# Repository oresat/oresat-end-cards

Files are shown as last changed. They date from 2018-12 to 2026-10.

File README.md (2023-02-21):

# "End Card" PCBs for OreSat

OreSat cards in the top position (#1) and bottom position (#20) are special because they interface with
both the solar arrays and with the end caps. They also tend to hold deployable antennas.

## Features

- 4 solar panel connectors
- 3 available RF connectors
- Alternative backplane connectors only (since the solar panel connectors take up the main connector spot)

## Connector information

- TBD.

## LICENSE

Copyright Portland State Aerospace Society 2022.

This documentation describes Open Hardware and is licensed under the CERN OHL v2

You may redistribute and modify this documentation under the terms of the CERN OHL v.1.2. [https://ohwr.org/cernohl](https://ohwr.org/cernohl). This documentation is distributed WITHOUT ANY EXPRESS OR IMPLIED WARRANTY, INCLUDING OF MERCHANTABILITY, SATISFACTORY QUALITY AND FITNESS FOR A PARTICULAR PURPOSE. Please see the CERN OHL v2 for applicable conditions.

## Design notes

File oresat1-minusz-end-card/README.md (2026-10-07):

---
title: "**OreSat1 -Z End Card**"
subtitle: |
  **Fabrication and Assembly Information**\
  For build TIME-STAMP
fontsize: 10pt
geometry:
  - margin=0.5in
toc: true
toc-depth: 2
colorlinks: true
urlcolor: blue
---

\newpage

# About this Board

## Board Description

The OreSat1 -Z End Card fits in the very "bottom" slot (Slot #20?) in the OreSat1 2U backplane. It's special because it hosts whatever antenna is on the -Z face of the satellite, which in this case is an L band monopole, a UHF band monopole, and an L1 band GPS patch antenna. The -Z End Card:

- Connects to the backplane with a main connector and three RF SMPM connectors
- Connects two -Z solar modules to the backplane (two of the solar module spots are taken up by the copper radiator panels for the CFC assembly)
- Routes an SMPM connector to a U.FL connector to jump up to the -Z End Cap's L1 band GPS patch antenna
- Has an OPD circuit to control:
   - Deploying the monopole antennas
   - Switching C3-UART to any of the -Z solar modules

## Documentation Links

- -Z End Card Git repository: <https://github.com/oresat/oresat-end-cards>
- **TODO:** -Z End Card Design Notes + Design Review Notes

## Documentation Files

| Filename | Notes |
| --- | --- |
| README.pdf | This README file |
| PROJECT-NAME-outline.dxf | Board outline (with holes) in DXF format |
| PROJECT-NAME-pcba.step | 3D model of PCBA (with components) |
| PROJECT-NAME-render-bot.jpg | Render of the top of the 3D model |
| PROJECT-NAME-render-bot.jpg | Render of the bottom of the 3D model |
| PROJECT-NAME-schematic.pdf | PDF of board schematics |

## Contact Information

- Website: <https://www.oresat.org/>
- Email: <oresat@pdx.edu>
- Instagram: @pdxaerospace

## Board Renders

Render of the top of the 3D model
Render of the bottom of the 3D model

\newpage

# Printed Circuit Board (PCB) Fabrication Information

## Board Info

- 4 layer board
- Bounding box is 99.8 x 94.6 mm (3.93 x 3.72 in)
- Board thickness is 1.59 mm (0.063 inch)
- **Important:** See Materials and Stack Up sections below

## Board Requirements

- Design Rules
    - Minimum Trace / Space design rules
       - Outer layers: 0.127 mm (5.0 mil) / 0.127 mm (5.0 mil)
       - Inner layers: 0.127 mm (5.0 mil) / 0.127 mm (5.0 mil)
    - Outer dimension router tolerance: +/- 0.254 mm (10.0 mil)
    - Hole placement tolerance: +/- 0.075 mm (3.0 mil)
    - Inner tab routed slot tolerance: +/- 0.254 mm (10.0 mil)
- Drills
   - Drill Positional Tolerance: 0.051 mm (2.0 mil)
   - Drill Size tolerance: +/- 0.064 mm (2.5 mil)
- Plated/Un-plated holes
  - There are 16 un-plated (NPT) holes
  - There are 434 plated through (PTH) holes
  - PTH minimum diameter: 0.254 mm (10 mil)
  - PTH minimum annulus: 0.102 mm (4 mil) radius
- Outline/Routing
  - Requires a 1.0 mm or smaller diameter routing bit
- Slots
  - There are two 1.0 mm plated slots.
- Cutouts
  - There is are two cutouts.
- There are 3 fiducials on the top layer and 3 fiducials on the bottom layer.
- Panel tabs ("mouse bites")
   - Card edges must be smooth; no mouse bites or other intrusions into the card outline.
   - If external mouse bites are required, minimize and customer will remove by hand before assembly.
- If not otherwise specified, build to IPC 6012 Class 2 or better.

## Materials

- Controlled impedance
   - The stackup is critical for the performance of high speed signals on this board.
   - As long as the stackup is controlled, the board is not considered controlled impedance.
- Isola FR408HR or material with equivalent Dk.
- Board Surface treatment should be ENIG, althogh immersion Silver is acceptable.
- White silkscreen on top and bottom surface
- Taiyo PSR-4000 or equivalent soldermask on top and bottom, no requirements for color.

## Stack Up

| Layer | Thickness | Notes |
|---|---|---|
| Top Copper | 0.043 mm /  1.7 mil |  Layer 1 foil, 1 oz Cu after plating |
| prepreg | 0.200 mm /  7.9 mil |  Prepreg - Isola FR408HR 2113 |
| Layer 2 | 0.018 mm /  0.7 mil |  Layer 2 foil, 0.5 oz Cu |
| Core | 0.991 mm / 39 mil |  Core Isola FR408HR |
| Layer 3 | 0.018 mm /  0.7 mil |  Layer 3 foil, 0.5 oz Cu |
| prepreg | 0.200 mm /  7.9 mil |  Prepreg - Isola FR408HR 2113 |
| Bottom Copper | 0.043 mm /  1.7 mil |  Layer 4 foil, 1 oz copper after plating |
| **Total Stackup** | **1.588 mm / 62.5 mil** | |

## Array / Panel Information

- Coordinate with Contract Manufacturer (CM) for optimal size of this panel.
- If no feedback from CM, then produce single boards (no panel).

## Fabrication Files

### IPC-2581 File

| Filename | Notes |
| --- | --- |
| PROJECT-NAME-ipc2581.xml | IPC-2581 board information file |

### Legacy PCB Files

| Filename | Notes |
| ---| --- |
| PROJECT-NAME-Edge_Cuts.gbr | RS274X file for the dimension (outline) layer |
| PROJECT-NAME-F_Silkscreen.gbr | RS274X file for the top silkscreen |
| PROJECT-NAME-F_Mask.gbr | RS274X file for the top soldermask |
| PROJECT-NAME-F_Cu.gbr | RS274X file for the top copper layer |
| PROJECT-NAME-In1_Cu.gbr | RS274X file for the layer 2 copper |
| PROJECT-NAME-In2_Cu.gbr | RS274X file for the layer 3 copper |
| PROJECT-NAME-B_Cu.gbr | RS274X file for the bottom copper layer |
| PROJECT-NAME-B_Mask.gbr | RS274X file for the bottom soldermask |
| PROJECT-NAME-B_Silkscreen.gbr | RS274X file for the bottom silkscreen |
| PROJECT-NAME-NPTH.drl | Excellon file for non-plated through holes |
| PROJECT-NAME-PTH.drl | Excellon file for plated through holes | 

\newpage

# Printed Circuit Board Assembly (PCBA) Information

## Assembly Info

- Components are on the top and bottom side of the board.
- This PCBA is mostly surface mount (SMT) with a few (THT) components.

## Assembly Requirements

- Assemble to IPC Class 2 or better
- Bake components that are not moisture sealed to appropriate levels as required.
- Solder paste MUST be leaded.
- Aqueous flux and wash strongly preferred.
   - Clean to NASA Standard "Visibly Clean (VC)": No particles or residues are visible to the naked eye.
- No conformal coating.
- Ship in antistatic protective bag

## Component Specific Assembly Information

- SMPM connectors (CM1 - CM3) should be hand-addedaccording to SOP (there is no solder paste for their footprints).
- Monopole antennas must be hand added according to the Antenna SOP.
- Resistor R1 must be hand added according to the OreSat End Card Deployment Resistor Mounting SOP.
- Press fit nuts HW1 - HW6 may be *carefully* added after SMT assembly is completed.

## Assembly Files

### IPC-2581 File

| Filename | Notes |
| --- | --- |
| PROJECT-NAME-ipc2581.xml | IPC-2581 board information file |

### Bill of Materials (BOM)

| Filename | Description |
| --- | --- |
| PROJECT-NAME-bom.csv | BOM in Comma Separated Variable format |

### Solder Paste Stencils

| Filename | Notes |
| --- | --- |
| PROJECT-NAME-B_Paste.gbr | RS274X file for top/front solder paste stencil |
| PROJECT-NAME-F_Paste.gbr | RS274X file for bottom/back solder paste stencil |

### Mounting/Placement Location

| Filename | Description |
| --- | --- |
| PROJECT-NAME-3u.pos | Pick and place locations for components |

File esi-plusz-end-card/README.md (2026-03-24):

---
title: "**OreSat1 +Z End Card**"
subtitle: |
  **Fabrication and Assembly Information**\
  For build TIME-STAMP
fontsize: 10pt
geometry:
  - margin=0.5in
toc: true
toc-depth: 2
colorlinks: true
urlcolor: blue
---

\newpage

# About this Board

## Board Description

The +Z End Card fits in the very "top" slot (Slot #1) in the OreSat backaplane. It's special because it hosts whatever antenna is on the +Z face, and also interfaces with the solar modules on the +Z "U" of the CubeSat. The +Z End Card:

- Connects to the backplane with a main connector and two RF SMPM connectors
- Connects four +Z solar modules to the backplane
- Mounts and matches to the S band helical antenna
- Routes an SMPM connector to a U.FL connector to jump up to the +Z End Cap's S band patch antenna
- Has an OPD circuit to control:
   - Deploying the helical antenna
   - Switching C3-UART to any of the +Z solar modules

## Documentation Links

- +Z End Card Git repository: <https://github.com/oresat/oresat-end-cards>
- **TODO:** +Z End Card Design Notes + Design Review Notes

## Documentation Files

| Filename | Notes |
| --- | --- |
| README.pdf | This README file |
| PROJECT-NAME-outline.dxf | Board outline (with holes) in DXF format |
| PROJECT-NAME-pcba.step | 3D model of PCBA (with components) |
| PROJECT-NAME-render-bot.jpg | Render of the top of the 3D model |
| PROJECT-NAME-render-bot.jpg | Render of the bottom of the 3D model |
| PROJECT-NAME-schematic.pdf | PDF of board schematics |

## Contact Information

- Website: <https://www.oresat.org/>
- Email: <oresat@pdx.edu>
- Instagram: @pdxaerospace

## Board Renders

Render of the top of the 3D model
Render of the bottom of the 3D model

\newpage

# Printed Circuit Board (PCB) Fabrication Information

## Board Info

- 4 layer board
- Bounding box is 99.8 x 94.6 mm (3.93 x 3.72 in)
- Board thickness is 1.59 mm (0.063 inch)
- **Important:** See Materials and Stack Up sections below

## Board Requirements

- Design Rules
    - Minimum Trace / Space design rules
       - Outer layers: 0.127 mm (5.0 mil) / 0.127 mm (5.0 mil)
       - Inner layers: 0.127 mm (5.0 mil) / 0.127 mm (5.0 mil)
    - Outer dimension router tolerance: +/- 0.254 mm (10.0 mil)
    - Hole placement tolerance: +/- 0.075 mm (3.0 mil)
    - Inner tab routed slot tolerance: +/- 0.254 mm (10.0 mil)
- Drills
   - Drill Positional Tolerance: 0.051 mm (2.0 mil)
   - Drill Size tolerance: +/- 0.064 mm (2.5 mil)
- Plated/Un-plated holes
  - There are 35 un-plated (NPT) holes
  - There are 454 plated through (PTH) holes
  - PTH minimum diameter: 0.254 mm (10 mil)
  - PTH minimum annulus: 0.102 mm (4 mil) radius
- Outline/Routing
  - Requires a 1.0 mm or smaller diameter routing bit
- Slots
  - There are no slots.
- Cutouts
  - There is one cutout
- There are 3 fiducials on the top layer.
- Panel tabs ("mouse bites")
   - Card edges must be smooth; no mouse bites or other intrusions into the card outline.
   - If external mouse bites are required, minimize and customer will remove by hand before assembly.
- If not otherwise specified, build to IPC 6012 Class 2 or better.

## Materials

- Controlled impedance
   - The stackup is critical for the performance of high speed signals on this board.
   - As long as the stackup is controlled, the board is not considered controlled impedance.
- Isola FR408HR or material with equivalent Dk.
- Board Surface treatment should be ENIG, althogh immersion Silver is acceptable.
- White silkscreen on top and bottom surface
- Taiyo PSR-4000 or equivalent soldermask on top and bottom, no requirements for color.

## Stack Up

| Layer | Thickness | Notes |
|---|---|---|
| Top Copper | 0.043 mm /  1.7 mil |  Layer 1 foil, 1 oz Cu after plating |
| prepreg | 0.200 mm /  7.9 mil |  Prepreg - Isola FR408HR 2113 |
| Layer 2 | 0.018 mm /  0.7 mil |  Layer 2 foil, 0.5 oz Cu |
| Core | 0.991 mm / 39 mil |  Core Isola FR408HR |
| Layer 3 | 0.018 mm /  0.7 mil |  Layer 3 foil, 0.5 oz Cu |
| prepreg | 0.200 mm /  7.9 mil |  Prepreg - Isola FR408HR 2113 |
| Bottom Copper | 0.043 mm /  1.7 mil |  Layer 4 foil, 1 oz copper after plating |
| **Total Stackup** | **1.588 mm / 62.5 mil** | |

## Array / Panel Information

- Coordinate with Contract Manufacturer (CM) for optimal size of this panel.
- If no feedback from CM, then produce single boards (no panel).

## Fabrication Files

### IPC-2581 File

| Filename | Notes |
| --- | --- |
| PROJECT-NAME-ipc2581.xml | IPC-2581 board information file |

### Legacy PCB Files

| Filename | Notes |
| ---| --- |
| PROJECT-NAME-Edge_Cuts.gbr | RS274X file for the dimension (outline) layer |
| PROJECT-NAME-F_Silkscreen.gbr | RS274X file for the top silkscreen |
| PROJECT-NAME-F_Mask.gbr | RS274X file for the top soldermask |
| PROJECT-NAME-F_Cu.gbr | RS274X file for the top copper layer |
| PROJECT-NAME-In1_Cu.gbr | RS274X file for the layer 2 copper |
| PROJECT-NAME-In2_Cu.gbr | RS274X file for the layer 3 copper |
| PROJECT-NAME-B_Cu.gbr | RS274X file for the bottom copper layer |
| PROJECT-NAME-B_Mask.gbr | RS274X file for the bottom soldermask |
| PROJECT-NAME-B_Silkscreen.gbr | RS274X file for the bottom silkscreen |
| PROJECT-NAME-NPTH.drl | Excellon file for non-plated through holes |
| PROJECT-NAME-PTH.drl | Excellon file for plated through holes | 

\newpage

# Printed Circuit Board Assembly (PCBA) Information

## Assembly Info

- All components are on the top side of the board.
- This PCBA is mostly surface mount (SMT) with a few (THT) components.

## Assembly Requirements

- Assemble to IPC Class 2 or better
- Bake components that are not moisture sealed to appropriate levels as required.
- Solder paste MUST be leaded.
- Aqueous flux and wash strongly preferred.
   - Clean to NASA Standard "Visibly Clean (VC)": No particles or residues are visible to the naked eye.
- No conformal coating.
- Ship in antistatic protective bag

## Component Specific Assembly Information

- SMPM connectors (CM1, CM2) should be hand-added (there is no solder paste for their footprints).
- HELICAL_ANT must be hand added according to the Helical Antenna SOP.
- Resistor R1 must be hand added according to the OreSat End Card Deployment Resistor Mounting SOP.
- Press fit nuts may be *carefully* added after SMT assembly is completed, although it's better if they're added before assembly.

## Assembly Files

### IPC-2581 File

| Filename | Notes |
| --- | --- |
| PROJECT-NAME-ipc2581.xml | IPC-2581 board information file |

### Bill of Materials (BOM)

| Filename | Description |
| --- | --- |
| PROJECT-NAME-bom.csv | BOM in Comma Separated Variable format |

### Solder Paste Stencils

| Filename | Notes |
| --- | --- |
| PROJECT-NAME-B_Paste.gbr | RS274X file for top/front solder paste stencil |
| PROJECT-NAME-F_Paste.gbr | RS274X file for bottom/back solder paste stencil |

### Mounting/Placement Location

| Filename | Description |
| --- | --- |
| PROJECT-NAME-3u.pos | Pick and place locations for components |

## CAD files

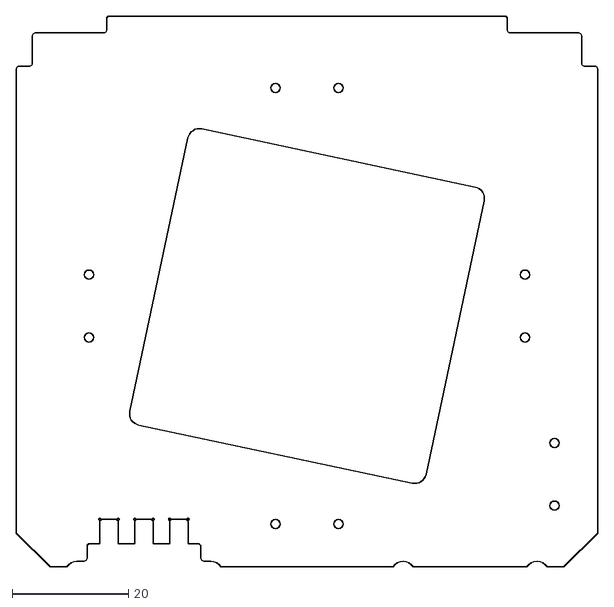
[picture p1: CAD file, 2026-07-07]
esi-plusz-end-card/Endcard PCB for beecon.dxf
99.8 x 94.6

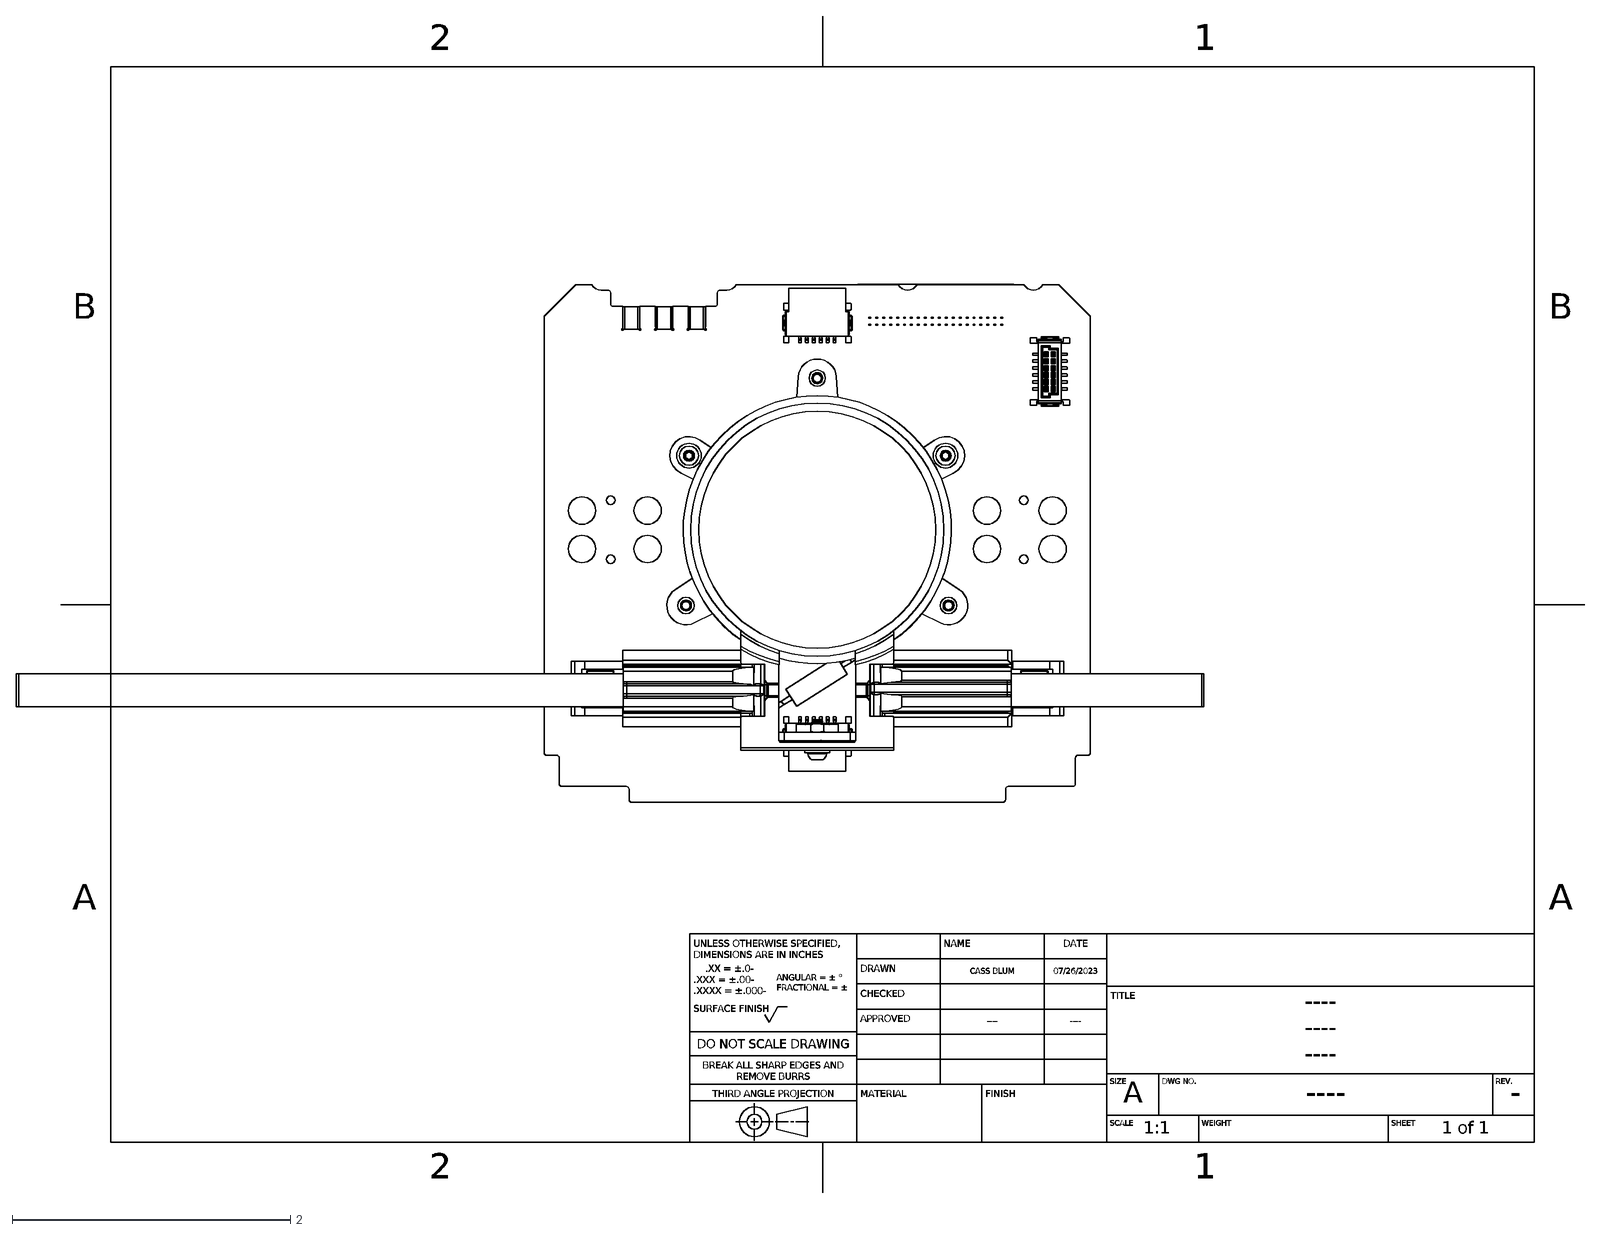
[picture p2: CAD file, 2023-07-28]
oresat0.5-minusz-end-card/oresat0.5-minusz-end-card.dxf
2
1
A
B
UNLESS OTHERWISE SPECIFIED, DIMENSIONS ARE IN INCHES
.XX = ±.0- .XXX = ±.00- .XXXX = ±.000-
ANGULAR = ± ° FRACTIONAL = ±
SURFACE FINISH
DO NOT SCALE DRAWING
BREAK ALL SHARP EDGES AND REMOVE BURRS
THIRD ANGLE PROJECTION
NAME
DATE
DRAWN
CASS BLUM
07/26/2023
CHECKED
APPROVED
----
MATERIAL
FINISH
TITLE
SIZE
DWG NO.
REV.
-
SCALE
1:1
WEIGHT
SHEET
1 of 1

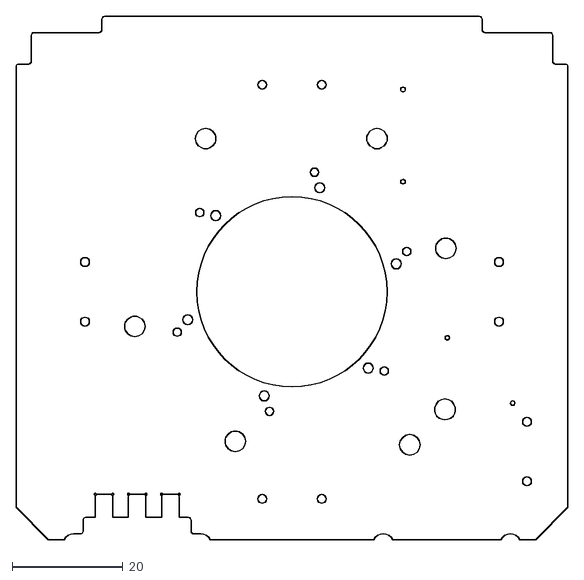
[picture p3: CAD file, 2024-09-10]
oresat0.5-plusz-end-card/Endcard PCBs - Endcard PCB (1).dxf
99.8 x 94.6

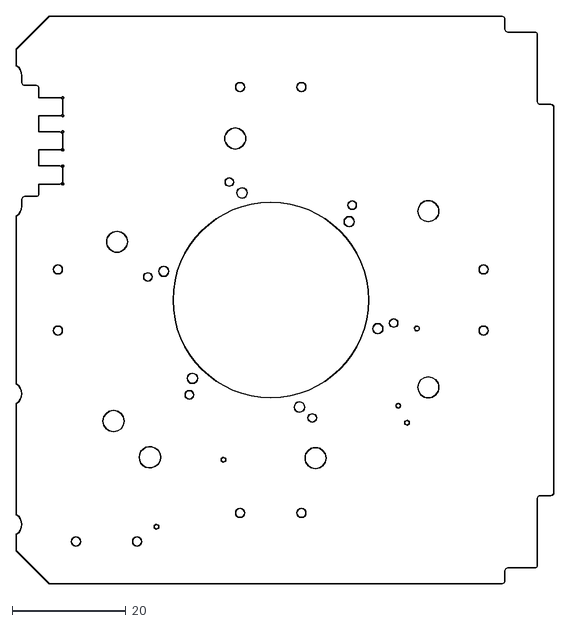
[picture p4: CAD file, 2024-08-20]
oresat0.5-plusz-end-card/oresat0.5-pluz-end-card.dxf
94.6 x 99.8

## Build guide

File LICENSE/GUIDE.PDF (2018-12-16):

# Guide to the CERN OHL v.1.2

This document contains guidelines on how to apply the CERN OHL v.1.2 to a given hardware design, and on the use of hardware designs licensed under the CERN OHL v.1.2.

How to apply the CERN OHL v.1.2 to a hardware design Pre-requisite:

Authorship/ownership of the design must be clear and undisputed. Only the legal owner of the rights in the hardware design may decide under what conditions to make it available. If ownership is vested in more than one person/entity, there must be an agreement among the owners to release the hardware design as open hardware, and under the CERN OHL in particular.

The hardware design documentation and files package

Pack all your hardware design documentation files (schematics, layout...) as well as the documents listed below in an archive file. This will ensure the licensee downloads everything in one go. It is best to archive the files using a format everybody can open. Schematics and layouts should be included in both source form and a format readable by everybody, such as pdf.

The following documents must be distributed together with the hardware design documentation:

- Document containing the CERN OHL v.1.2 (e.g. LICENSE.PDF)
- This Guide
- Text files (plain ASCII file), where information can be added to but not removed from, listing:
- Contact point wishing to receive information about manufactured Products (see section 4.2) (e.g. PRODUCT.TXT);
- Modifications made by Licensee (see section 3.4.b) (e.g. CHANGES.TXT)

What to do with the hardware design documentation

Include in the hardware design documentation, for instance as a header, the following elements (see section 3.1 CERN OHL v.1.2):
- a copyright notice reflecting actual ownership;
- a notice that the hardware design documentation is licensed under the CERN OHL v.1.2, possibly with a link to http://ohwr.org/cernohl where the licence texts are hosted:
- “Licensed under CERN OHL v.1.2 or later”
- “Licensed under CERN OHL v.1.2”;
- a disclaimer of warranties;
- a Documentation Location if you wish to specify one;

The following is an example of header if CERN is the Licensor:

Copyright CERN 2013.

This documentation describes Open Hardware and is licensed under the CERN OHL v. 1.2.

You may redistribute and modify this documentation under the terms of the CERN OHL v.1.2. (http://ohwr.org/cernohl). This documentation is distributed WITHOUT ANY EXPRESS OR IMPLIED WARRANTY, INCLUDING OF MERCHANTABILITY, SATISFACTORY QUALITY AND FITNESS FOR A PARTICULAR PURPOSE. Please see the CERN OHL v.1.2 for applicable conditions

Include in a part of the Documentation corresponding to a visible part of the Product (e.g. silkscreen or top copper for a Printed Circuit Board):

- the licence notice: “Licensed under CERN OHL v.1.2”
- Do not include the CERN logo or the copyright notice
- the Documentation Location if you wish it to appear on the Product, thus enabling all subsequent recipients of the Products to find the Documentation.

How to deal with hardware designs licensed under the CERN OHL v.1.2
Generally speaking, you must always comply with any obligations applying to a particular design (detailed in a contract or accompanying licence). If you receive hardware designs licensed under the CERN OHL v.1.2, the obligations are to:
- Keep intact all the copyright and trademark notices and Documentation Location notices that are on the hardware design documentation;
- Keep intact the references to the CERN OHL v.1.2;
- Keep intact the disclaimer of warranties.

If you modify hardware design that you received from someone else that is licensed under the CERN OHL v.1.2, you must

- Keep intact all the notices referred to above;
- Include notices that you have modified the hardware designs, detailing what modifications where made (e.g. in a CHANGES.TXT file);
- Add the appropriate copyright notice and Documentation Location to the modifications that were made;
- license the modifications under the CERN OHL v.1.2 if you distribute them.

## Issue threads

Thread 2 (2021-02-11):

50 ohm resistors are too big

davidalay, 2021-02-11:
footprint is 0805, should be 0603

Closed 2021-04-08.

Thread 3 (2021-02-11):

Bigger burn resistor package

davidalay, 2021-02-11:
Footprint for the burnwire resistor should be bigger, have larger drill holes, and oblong pads.  Also add second set of vias so we can J-bend the leads

Closed 2021-04-08.

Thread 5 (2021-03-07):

Move the antenna holes to center the holes on the tape spring antennas.

andrewgreenberg, 2021-03-07:
Bonus points if the mezzanine board doesn't have to be modified.

Closed 2021-04-08.

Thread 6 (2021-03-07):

Change melt wire resistor to 7.2 ohms

andrewgreenberg, 2021-03-07:
A 7.2 ohm melt wire resistor is 5 W at 6V and 10W at 8.4V.

Closed 2021-04-08.

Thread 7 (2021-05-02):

Fix the melt wire resistor and mezzanine board hybrids interference -- probably rev the placement of the hybrids on the mezzanine, not the footprint of the melt wire resistor.

davidalay, 2021-05-02:

Closed 2021-11-04.

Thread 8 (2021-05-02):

Larger annular ring around the wires (if it doesn't screw with RF stuff)

davidalay, 2021-05-02:

Closed 2021-11-04.

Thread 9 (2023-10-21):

Update all M2 press-fit nuts from a 3.7 mm to 4.0 mm hole

andrewgreenberg, 2023-10-21:
... which still is press fit, but doesn't pook out the board.

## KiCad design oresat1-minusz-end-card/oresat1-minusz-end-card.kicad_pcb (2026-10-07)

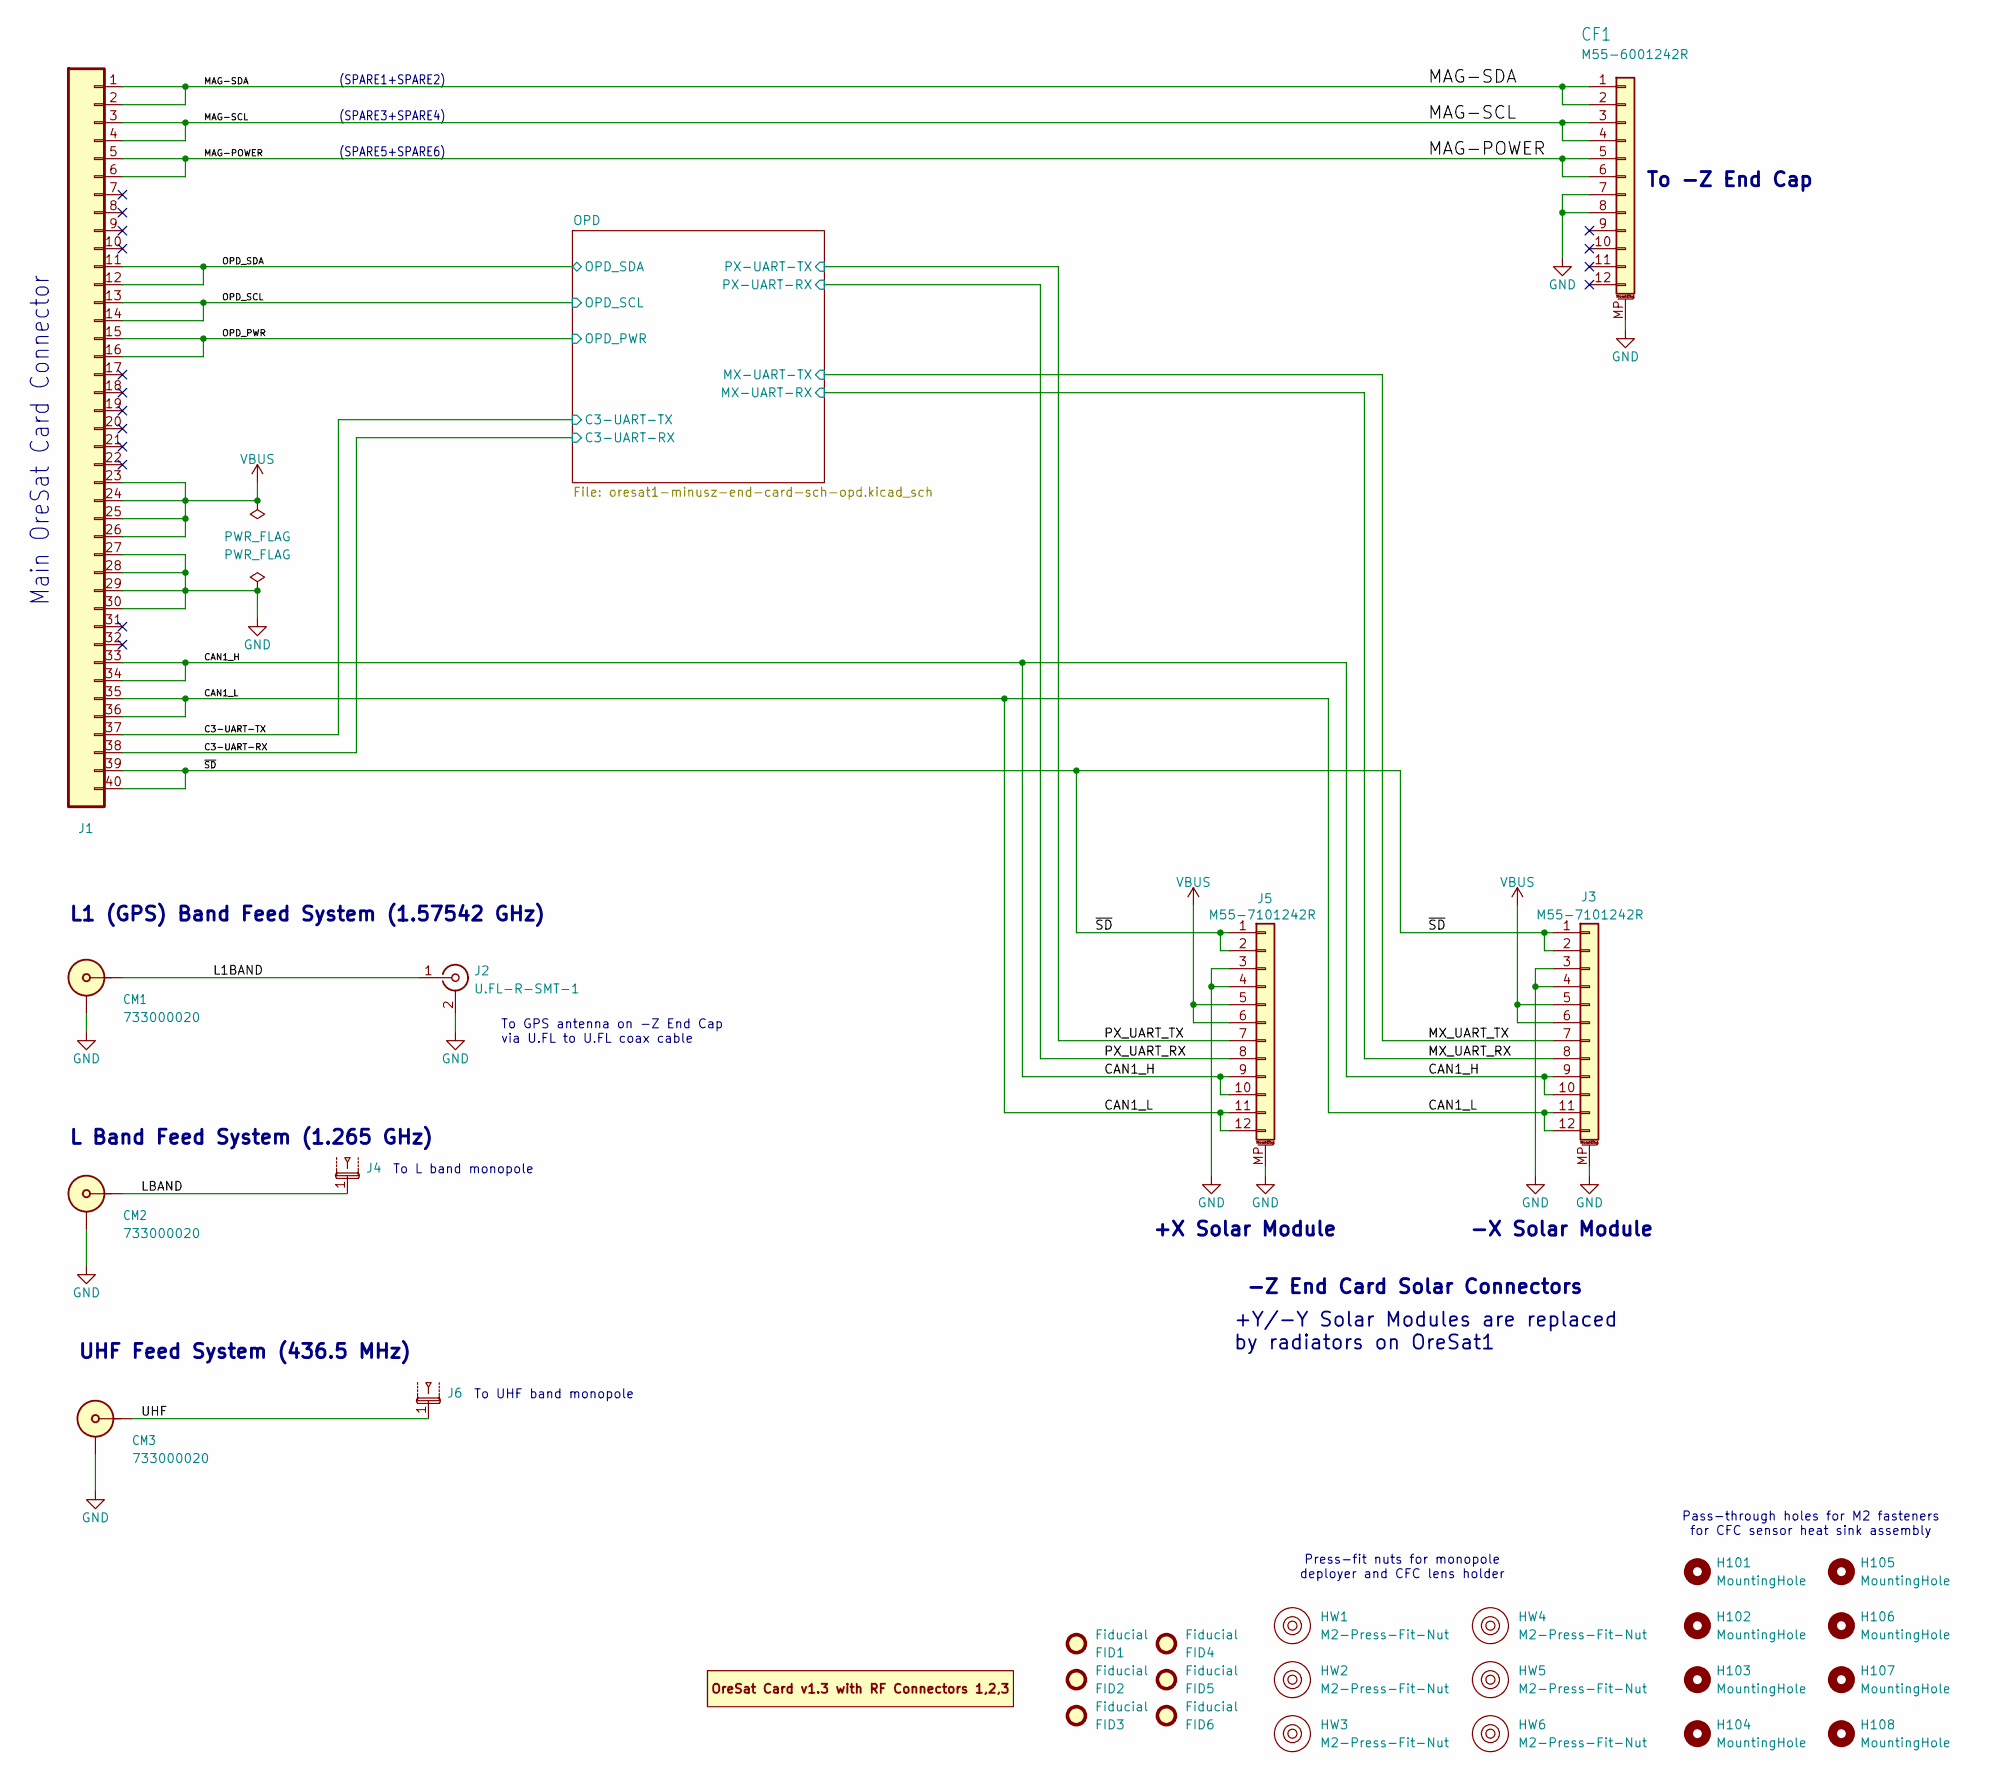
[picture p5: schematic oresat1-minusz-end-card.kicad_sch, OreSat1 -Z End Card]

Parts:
CF1: M55-6001242R; J-Harwin-M55-60X1242R; MPN M55-6001242R
CM1, CM2, CM3: 733000020; J-MOLEX-SMPM-073300-002X; MPN 2477330-1
FID1, FID2, FID3, FID4, FID5, FID6: Fiducial; Fiducial_1mm_Mask2mm
H101, H102, H103, H104, H105, H106, H107, H108: MountingHole; MountingHole_5mm
HW1, HW2, HW3, HW4, HW5, HW6: M2-Press-Fit-Nut; MPN N/A
J1: J-SAMTEC-TFM-120-01-L-D-RA; J-SAMTEC-TFM-120-X1-XXX-D-RA; MPN TFM-120-01-L-D-RA
J2: U.FL-R-SMT-1; U.FL_Hirose_U.FL-R-SMT-1_Vertical; MPN U.FL-R-SMT-1(10)
J3, J5: M55-7101242R; J-Harwin-M55-7101242R; MPN M55-7101242R
J4, J6: tape-measure-slot-antenna
PCB1: ORESAT-CARD-V1.3-GENERIC-3RF; ORESAT-CARD-V1.3-3RF

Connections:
/C3-UART-RX: J1.38; also elsewhere on the board
/C3-UART-TX: J1.37; also elsewhere on the board
/CAN1_H: J1.33, J1.34, J3.9, J3.10, J5.9, J5.10
/CAN1_L: J1.35, J1.36, J3.11, J3.12, J5.11, J5.12
/L1BAND: CM1.1 (SIG), J2.1 (In)
/LBAND: CM2.1 (SIG), J4.1
/MAG-POWER: CF1.5, CF1.6, J1.5, J1.6
/MAG-SCL: CF1.3, CF1.4, J1.3, J1.4
/MAG-SDA: CF1.1, CF1.2, J1.1, J1.2
/MX_UART_RX: J3.8; also elsewhere on the board
/MX_UART_TX: J3.7; also elsewhere on the board
/OPD_PWR: J1.15, J1.16; also elsewhere on the board
/OPD_SCL: J1.13, J1.14; also elsewhere on the board
/OPD_SDA: J1.11, J1.12; also elsewhere on the board
/PX_UART_RX: J5.8; also elsewhere on the board
/PX_UART_TX: J5.7; also elsewhere on the board
/UHF: CM3.1 (SIG), J6.1
/~SD: J1.39, J1.40, J3.1, J3.2, J5.1, J5.2
GND: CF1.7, CF1.8, CF1.MP (MountPin), CM1.2 (SHLD), CM2.2 (SHLD), CM3.2 (SHLD), J1.27, J1.28, J1.29, J1.30, J2.2 (Ext), J3.3, J3.4, J3.MP (MountPin), J5.3, J5.4, J5.MP (MountPin); also elsewhere on the board
VBUS: J1.23, J1.24, J1.25, J1.26, J3.5, J3.6, J5.5, J5.6; also elsewhere on the board

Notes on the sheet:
(SPARE5+SPARE6)
(SPARE3+SPARE4)
-Z End Card Solar Connectors
Pass-through holes for M2 fasteners for CFC sensor heat sink assembly
To L band monopole
+Y/-Y Solar Modules are replaced by radiators on OreSat1
+X Solar Module
Main OreSat Card Connector
Press-fit nuts for monopole deployer and CFC lens holder
To UHF band monopole
(SPARE1+SPARE2)
UHF Feed System (436.5 MHz)
L1 (GPS) Band Feed System (1.57542 GHz)
To -Z End Cap
To GPS antenna on -Z End Cap via U.FL to U.FL coax cable
L Band Feed System (1.265 GHz)
-X Solar Module

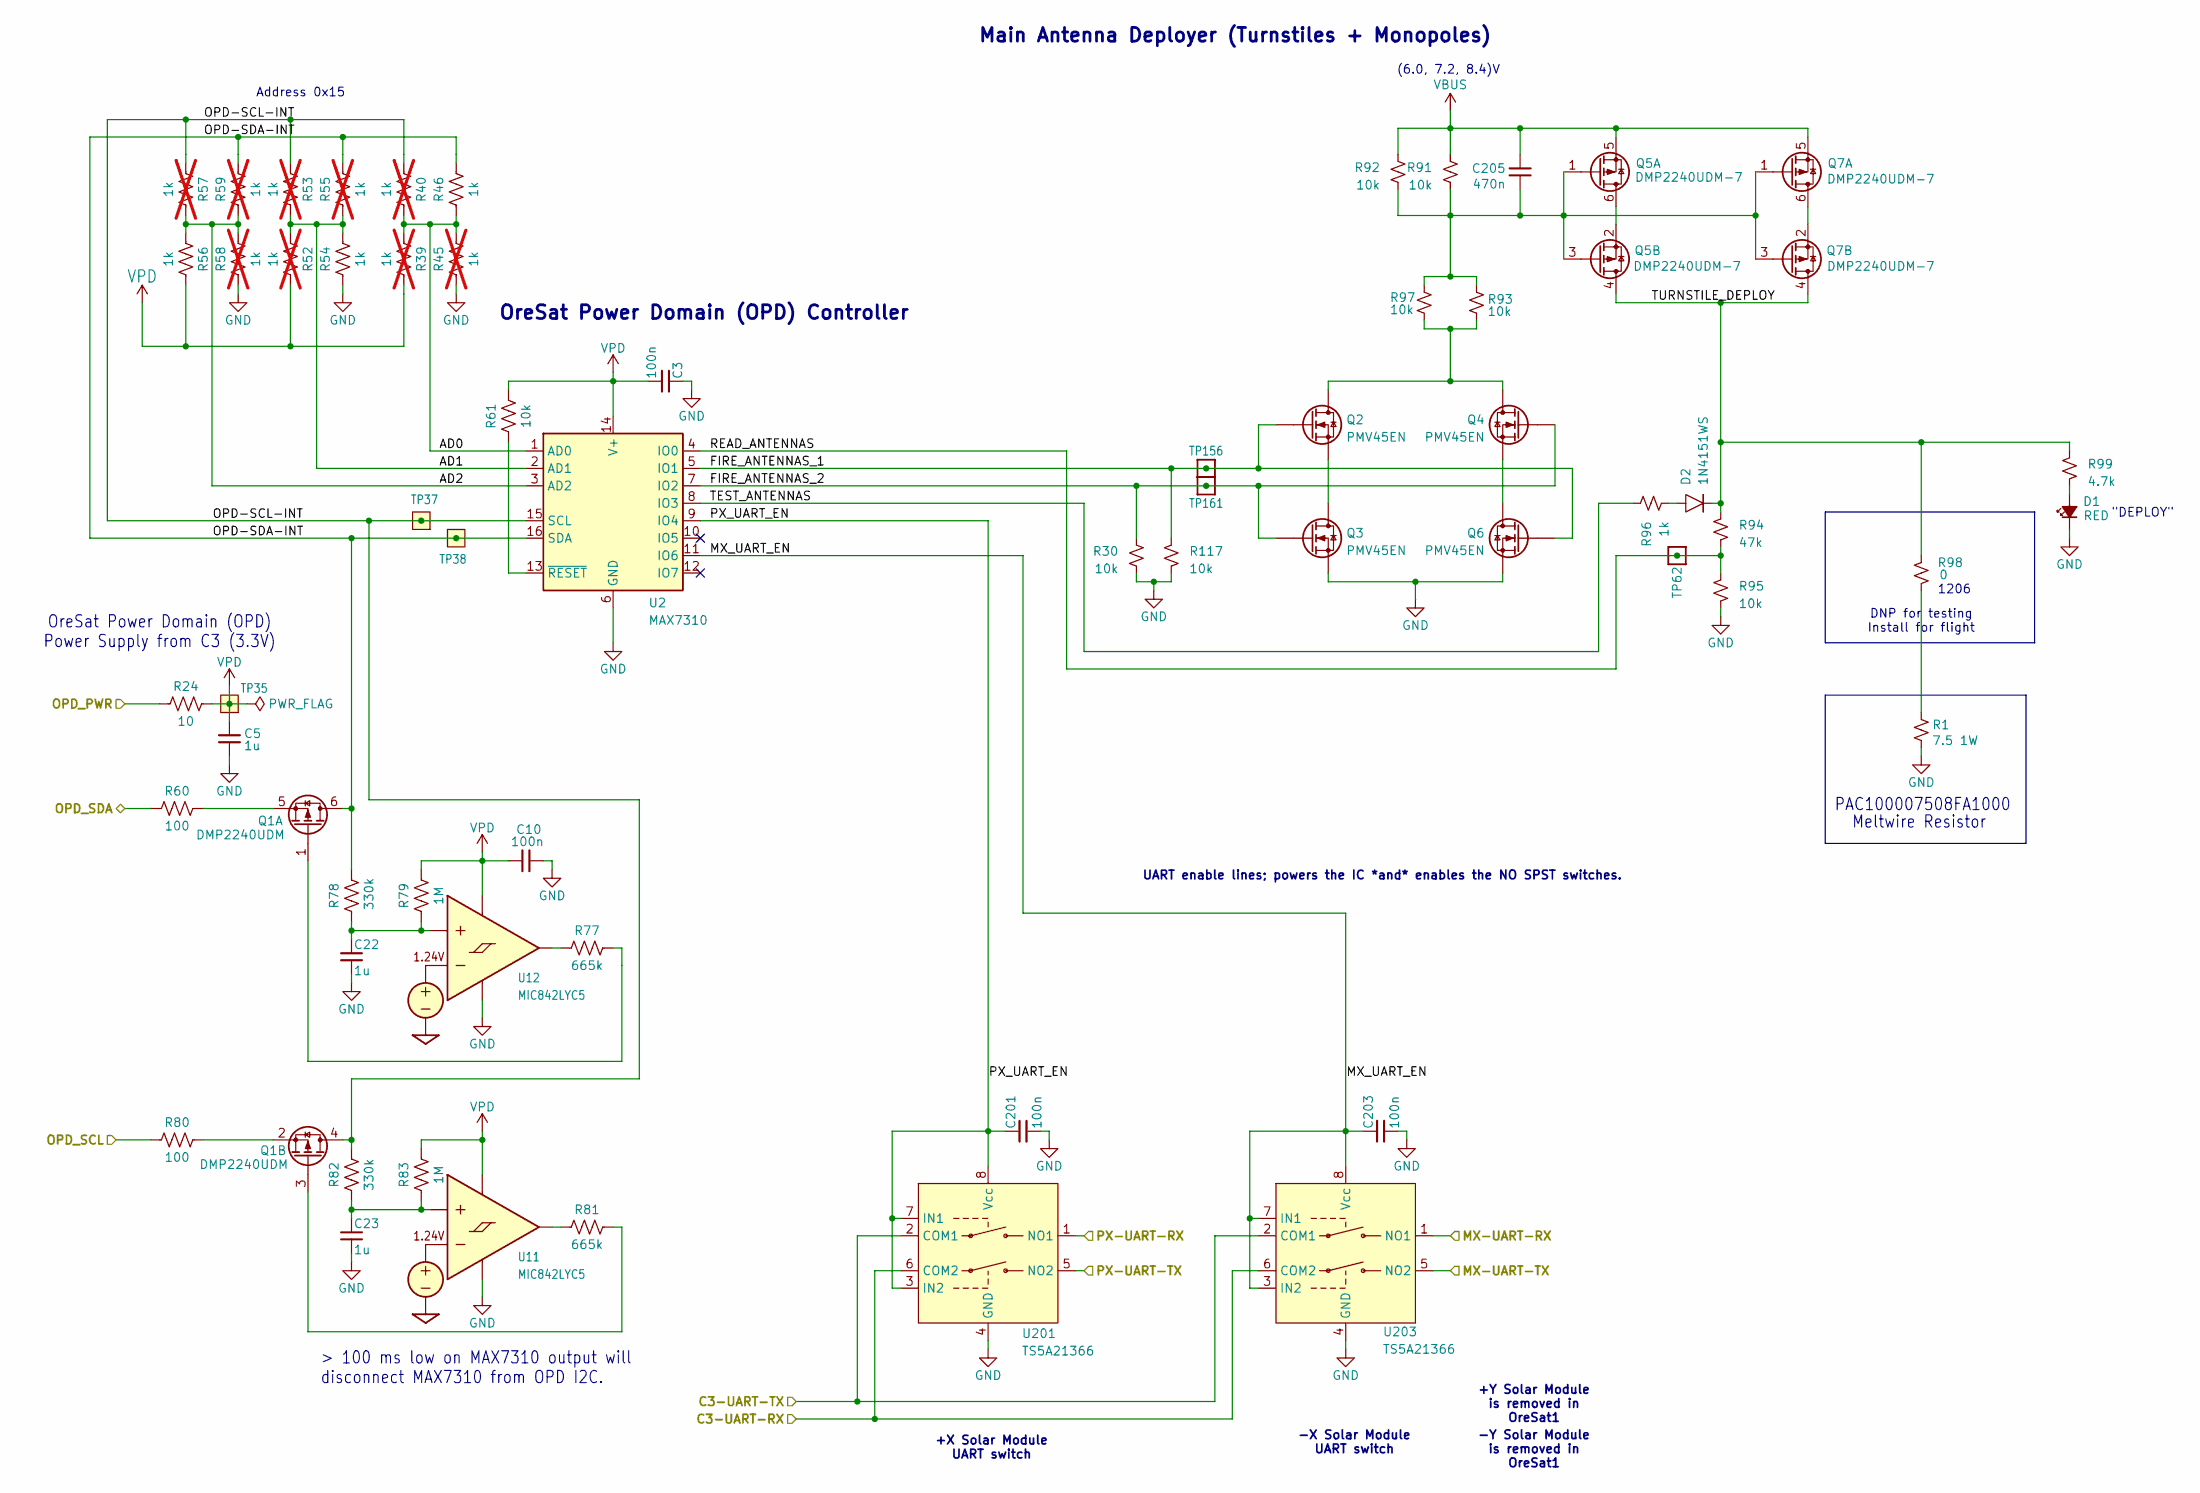
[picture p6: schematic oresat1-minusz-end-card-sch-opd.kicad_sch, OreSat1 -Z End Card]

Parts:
C3, C10, C201, C203: 100n; 0603-C-NOSILK; MPN C0603C104K5RACAUTO
C5, C22, C23: 1u; 0603-C-NOSILK; MPN GRT188R71E105KE13D
C205: 470n; 0603-C-NOSILK; MPN C0603C474K3RACAUTO
D1: RED; LED_0603_1608Metric; MPN 150060RS75000
D2: 1N4151WS; D_SOD-323; MPN 1N4151WS-E3-08
Q1: DMP2240UDM; SOT-23-6; MPN DMP2240UDM
Q2, Q3, Q4, Q6: PMV45EN; SOT-23-3; MPN PMV45EN2R
Q5, Q7: DMP2240UDM-7; SOT-23-6; MPN DMP2240UDM
R1: 7.5 1W; R-PAC100-FOR-MELTWIRE; MPN PAC100007508FA1000
R24: 10; 0603-C-NOSILK; MPN RMCF0603FT10R0
R30, R61, R91, R92, R93, R95, R97, R117: 10k; 0603-C-NOSILK; MPN RMCF0603FT10K0
R39, R40, R45, R52, R53, R55, R57, R58, R59: 1k; 0603-C-NOSILK; MPN RMCF0603FT1K00; not fitted
R46, R54, R56, R96: 1k; 0603-C-NOSILK; MPN RMCF0603FT1K00
R60, R80: 100; 0603-C-NOSILK; MPN RMCF0603FT100R
R77, R81: 665k; 0603-C-NOSILK; MPN RMCF0603FT665K
R78, R82: 330k; 0603-C-NOSILK; MPN RMCF0603FT330K
R79, R83: 1M; 0603-C-NOSILK; MPN RMCF0603FT1M00
R94: 47k; 0603-C-NOSILK; MPN RMCF0603FT47K0
R98: 0; 1206-C; MPN RMCF1206ZG0R00
R99: 4.7k; 0603-C-NOSILK; MPN RMCF0603FT4K70
TP35, TP37, TP38: Test-Point; TestPoint-0.75mm-th
TP62, TP156, TP161: Test-Point; TestPoint_Pad_D1.0mm
U2: MAX7310; QFN-16-1EP_4x4mm_P0.65mm_EP2.1x2.1mm; MPN MAX7310ATE+
U11, U12: MIC842LYC5; SOT-353_SC-70-5; MPN MIC842LYC5-TR
U201, U203: TS5A21366; VSSOP-8_2.3x2mm_P0.5mm; MPN TS5A21366DCUR

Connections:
/C3-UART-RX: U201.6 (COM2), U203.6 (COM2); also elsewhere on the board
/C3-UART-TX: U201.2 (COM1), U203.2 (COM1); also elsewhere on the board
/MX_UART_RX: U203.1 (NO1); also elsewhere on the board
/MX_UART_TX: U203.5 (NO2); also elsewhere on the board
/OPD/AD0: R39.1, R40.2, R45.2, R46.1, U2.1 (AD0)
/OPD/AD1: R52.1, R53.2, R54.2, R55.1, U2.2 (AD1)
/OPD/AD2: R56.1, R57.2, R58.2, R59.1, U2.3 (AD2)
/OPD/FIRE_ANTENNAS_1: Q2.1 (G), Q6.1 (G), R117.1, TP156.1 (1_1), U2.5 (IO1)
/OPD/FIRE_ANTENNAS_2: Q3.1 (G), Q4.1 (G), R30.1, TP161.1 (1_1), U2.7 (IO2)
/OPD/MX_UART_EN: C203.1, U2.11 (IO6), U203.3 (IN2), U203.7 (IN1), U203.8 (Vcc)
/OPD/OPD-SCL-INT: Q1.4 (D), R40.1, R53.1, R57.1, R82.2, TP37.1 (1_1), U2.15 (SCL)
/OPD/OPD-SDA-INT: Q1.6 (D), R46.2, R55.2, R59.2, R78.2, TP38.1 (1_1), U2.16 (SDA)
/OPD/PX_UART_EN: C201.1, U2.9 (IO4), U201.3 (IN2), U201.7 (IN1), U201.8 (Vcc)
/OPD/READ_ANTENNAS: R94.2, R95.1, TP62.1 (1_1), U2.4 (IO0)
/OPD/TEST_ANTENNAS: R96.1, U2.8 (IO3)
/OPD/TURNSTILE_DEPLOY: D2.1, Q5.4 (D), Q7.4 (D), R94.1, R98.1, R99.1
/OPD_PWR: R24.1; also elsewhere on the board
/OPD_SCL: R80.1; also elsewhere on the board
/OPD_SDA: R60.1; also elsewhere on the board
/PX_UART_RX: U201.1 (NO1); also elsewhere on the board
/PX_UART_TX: U201.5 (NO2); also elsewhere on the board
GND: C3.1, C5.2, C10.1, C22.2, C23.2, C201.2, C203.2, D1.1 (K), Q3.2 (S), Q6.2 (S), R1.2, R30.2, R45.1, R54.1, R58.1, R95.2, R117.2, U2.6 (GND), U2.17 (GND), U11.2 (GND), U12.2 (GND), U201.4 (GND), U203.4 (GND); also elsewhere on the board
unnamed: D1.2 (A), R99.2
unnamed: D2.2, R96.2
unnamed: Q1.1 (G), R77.2
unnamed: Q1.5 (S), R60.2
unnamed: Q1.3 (G), R81.2
unnamed: Q1.2 (S), R80.2
unnamed: Q2.3 (D), Q4.3 (D), R93.1, R97.1
unnamed: Q2.2 (S), Q3.3 (D)
unnamed: Q4.2 (S), Q6.3 (D)
unnamed: Q5.2 (S), Q5.6 (D)
unnamed: C205.1, Q5.1 (G), Q5.3 (G), Q7.1 (G), Q7.3 (G), R91.2, R92.2, R93.2, R97.2
unnamed: Q7.2 (S), Q7.6 (D)
unnamed: R1.1, R98.2
unnamed: R61.1, U2.13 (~RESET)
unnamed: C23.1, R82.1, R83.1, U11.1 (INP)
unnamed: R81.1, U11.4 (OUT)
unnamed: C22.1, R78.1, R79.1, U12.1 (INP)
unnamed: R77.1, U12.4 (OUT)
VBUS: C205.2, Q5.5 (S), Q7.5 (S), R91.1, R92.1; also elsewhere on the board
VPD: C3.2, C5.1, C10.2, R24.2, R39.2, R52.2, R56.2, R61.2, R79.2, R83.2, TP35.1 (1_1), U2.14 (V+), U11.5 (VDD), U12.5 (VDD)

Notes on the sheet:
1206
-Y Solar Module is removed in OreSat1
UART enable lines; powers the IC *and* enables the NO SPST switches.
(6.0, 7.2, 8.4)V
Main Antenna Deployer (Turnstiles + Monopoles)
"DEPLOY"
Meltwire Resistor
+Y Solar Module is removed in OreSat1
-X Solar Module UART switch
DNP for testing Install for flight
OreSat Power Domain (OPD) Power Supply from C3 (3.3V)
OreSat Power Domain (OPD) Controller
> 100 ms low on MAX7310 output will disconnect MAX7310 from OPD I2C.
Address 0x15
+X Solar Module UART switch
PAC100007508FA1000

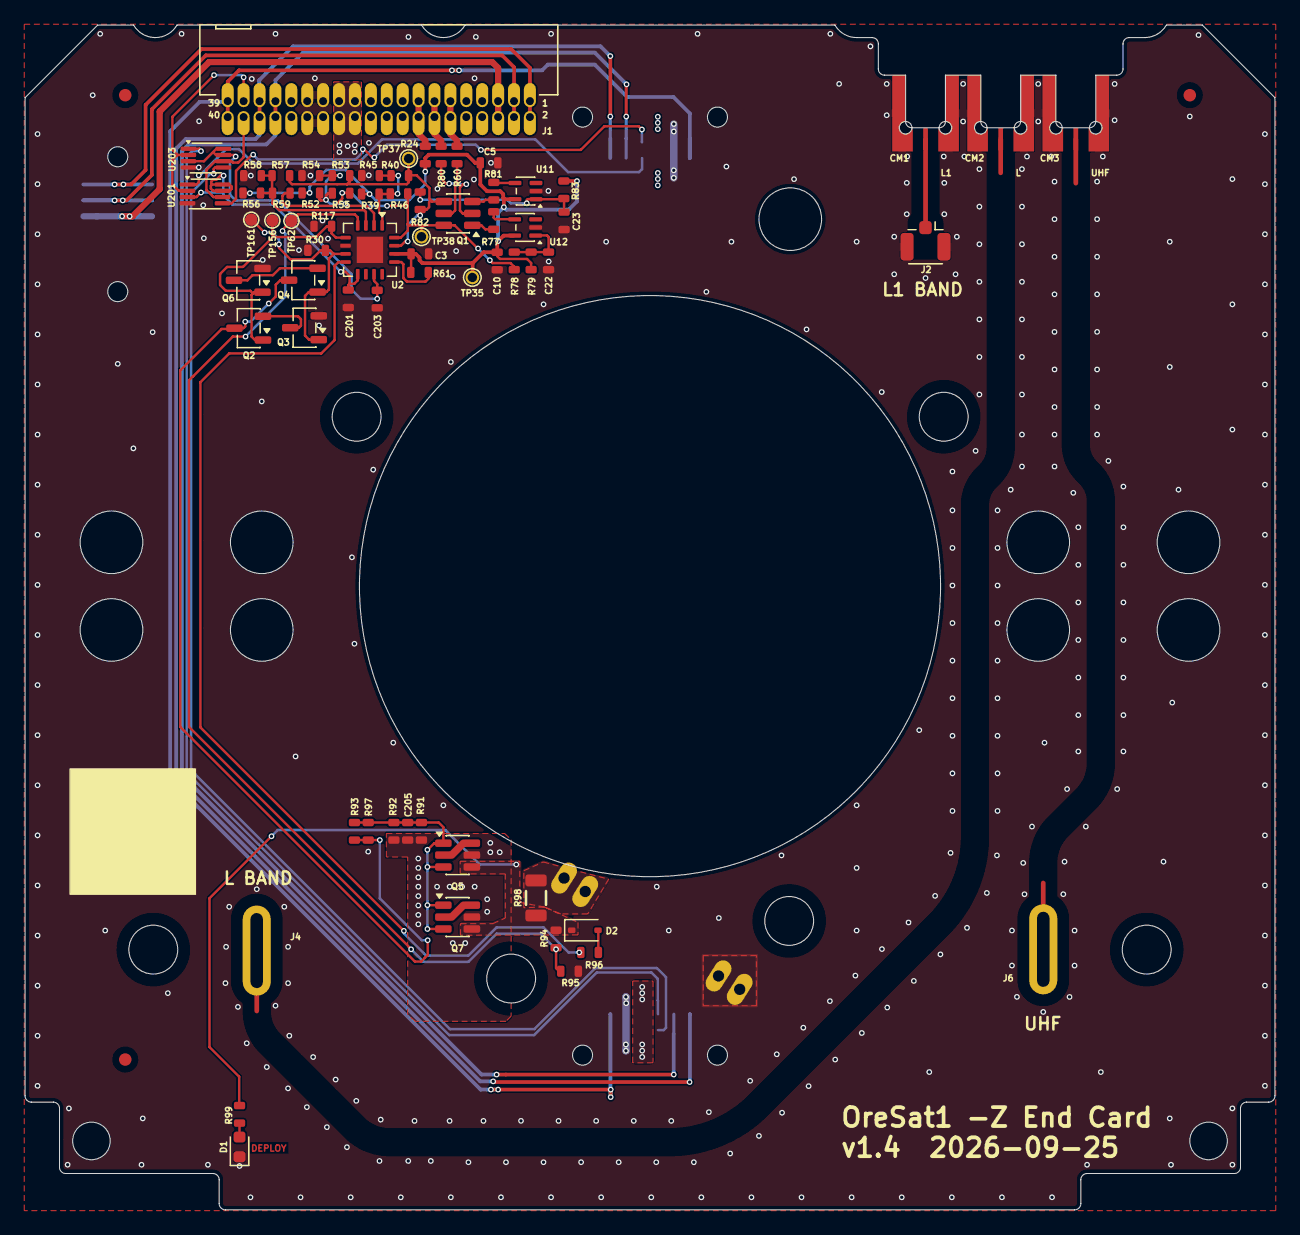
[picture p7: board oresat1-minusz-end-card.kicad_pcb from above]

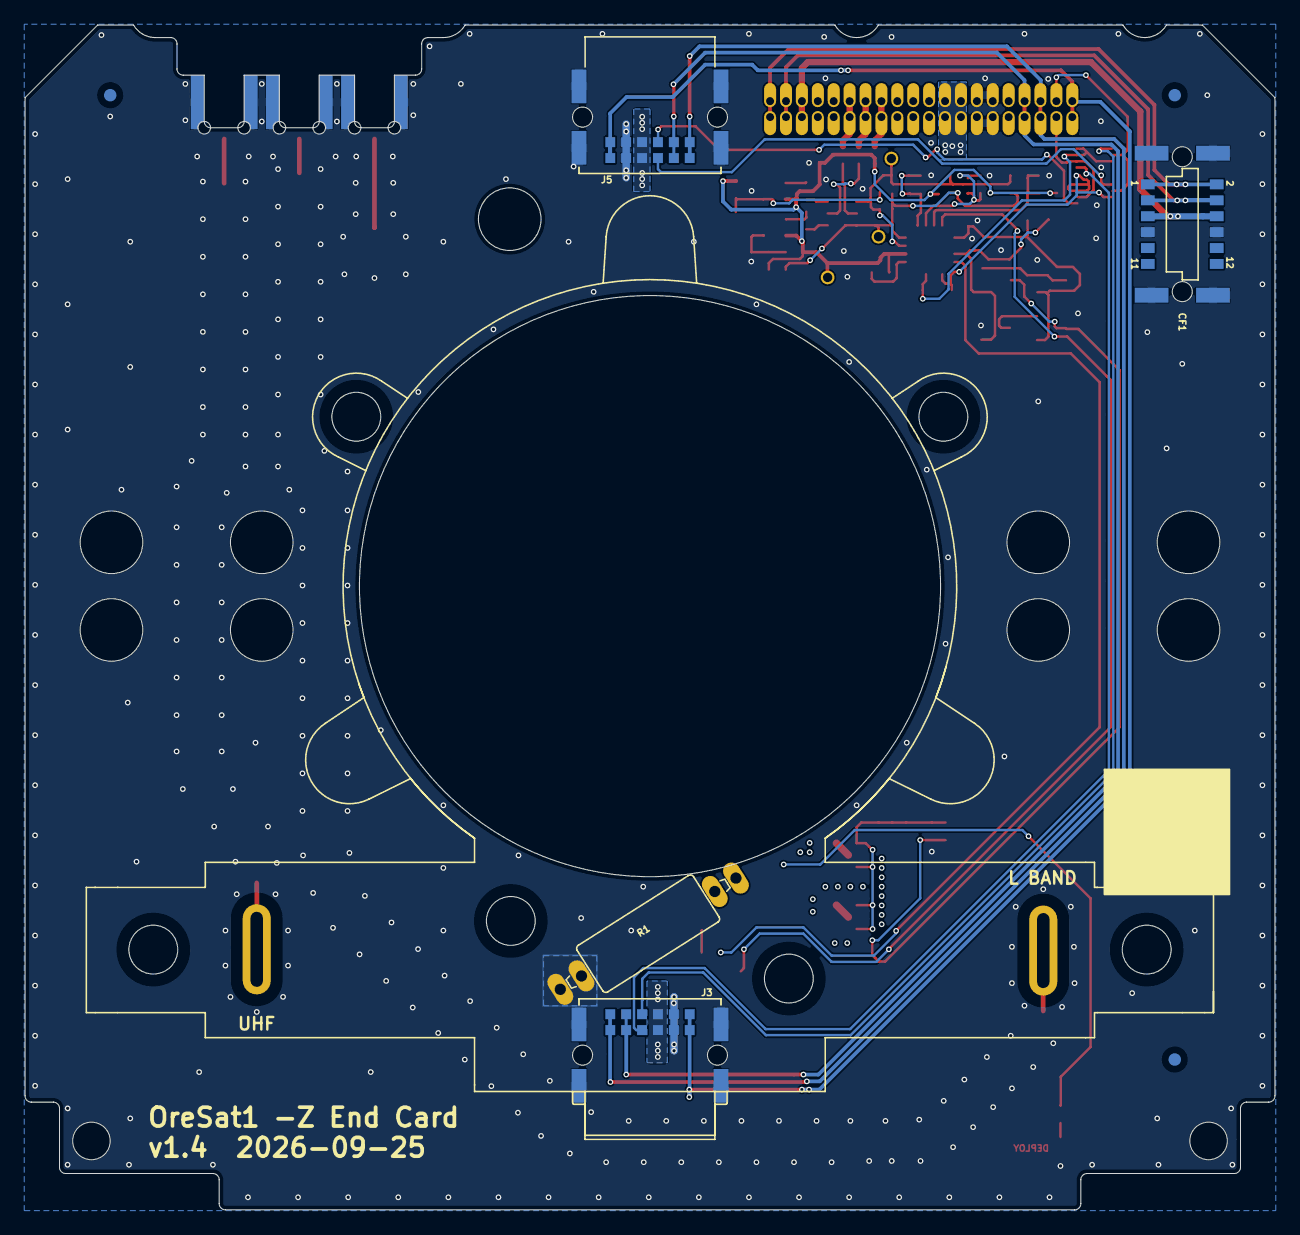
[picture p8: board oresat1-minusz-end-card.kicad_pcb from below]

Board: 4 copper layers, 99.8 x 94.6 mm, 93 parts (13 on the bottom side), 51 nets.

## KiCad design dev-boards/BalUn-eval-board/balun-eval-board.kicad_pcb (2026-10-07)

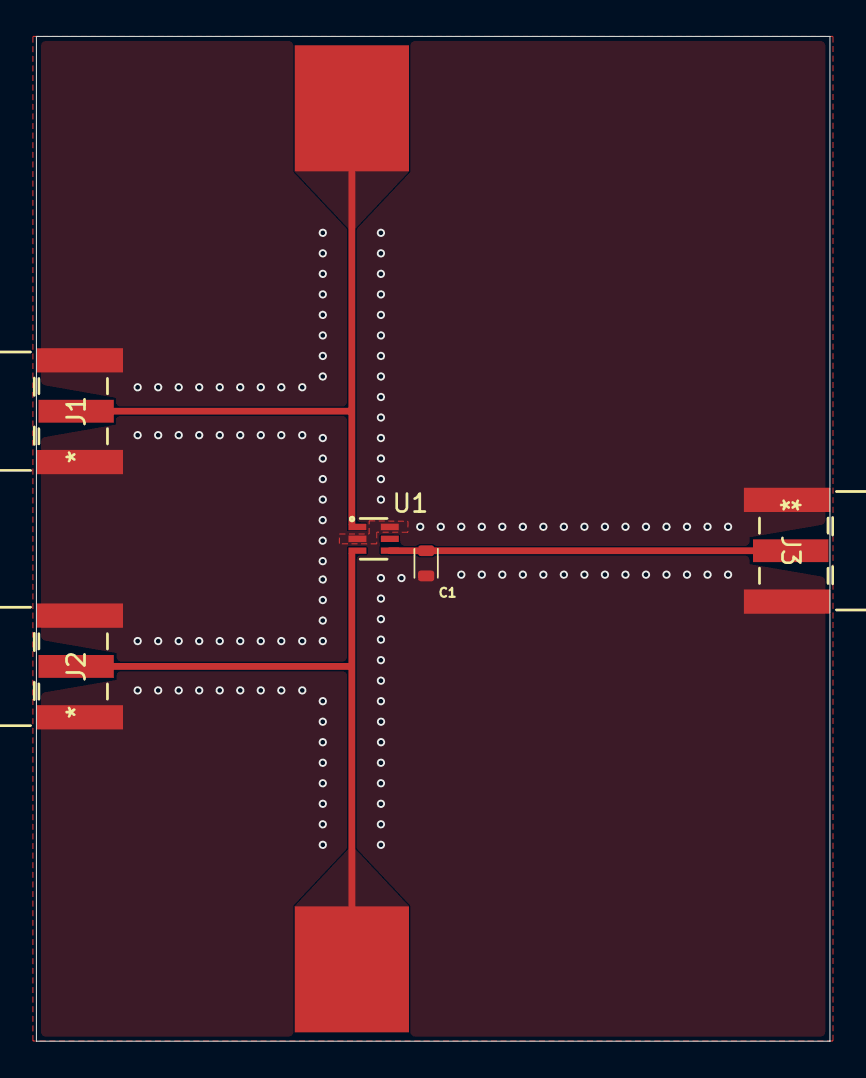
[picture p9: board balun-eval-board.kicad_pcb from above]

Board: 4 copper layers, 44.1 x 55.8 mm, 7 parts (0 on the bottom side), 4 nets.

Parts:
C1: C; 0603-C
J1, J2, J3: SMA-142-0711-201; SMA-J-P-H-ST-EM1
TP1, TP2: TestPoint_Pad_D1.0mm
U1: NCS2-62+; 2450FB15A050E_JOT

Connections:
GND: C1.1, J1.2 (In), J1.3 (Ext), J2.2 (In), J2.3 (Ext), J3.2 (In), J3.3 (Ext), U1.2 (GND), U1.6 (GND)
unnamed: C1.2, J3.1, U1.4
unnamed: J1.1, TP1.1 (1_1), U1.1
unnamed: J2.1, TP2.1 (1_1), U1.3

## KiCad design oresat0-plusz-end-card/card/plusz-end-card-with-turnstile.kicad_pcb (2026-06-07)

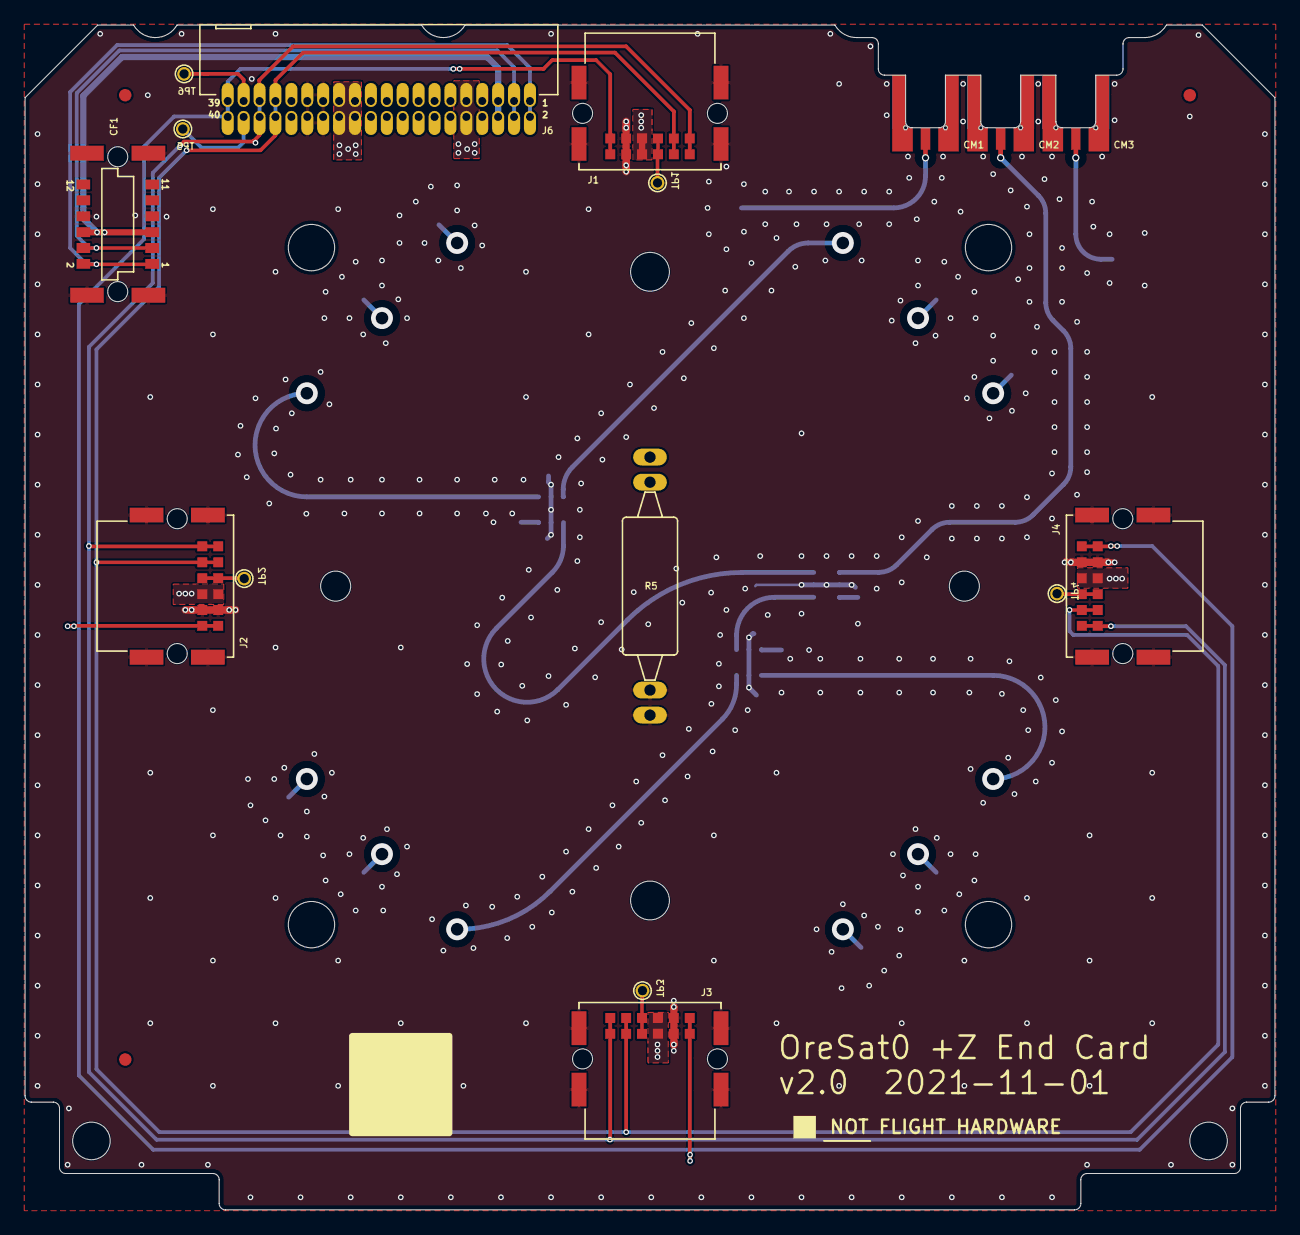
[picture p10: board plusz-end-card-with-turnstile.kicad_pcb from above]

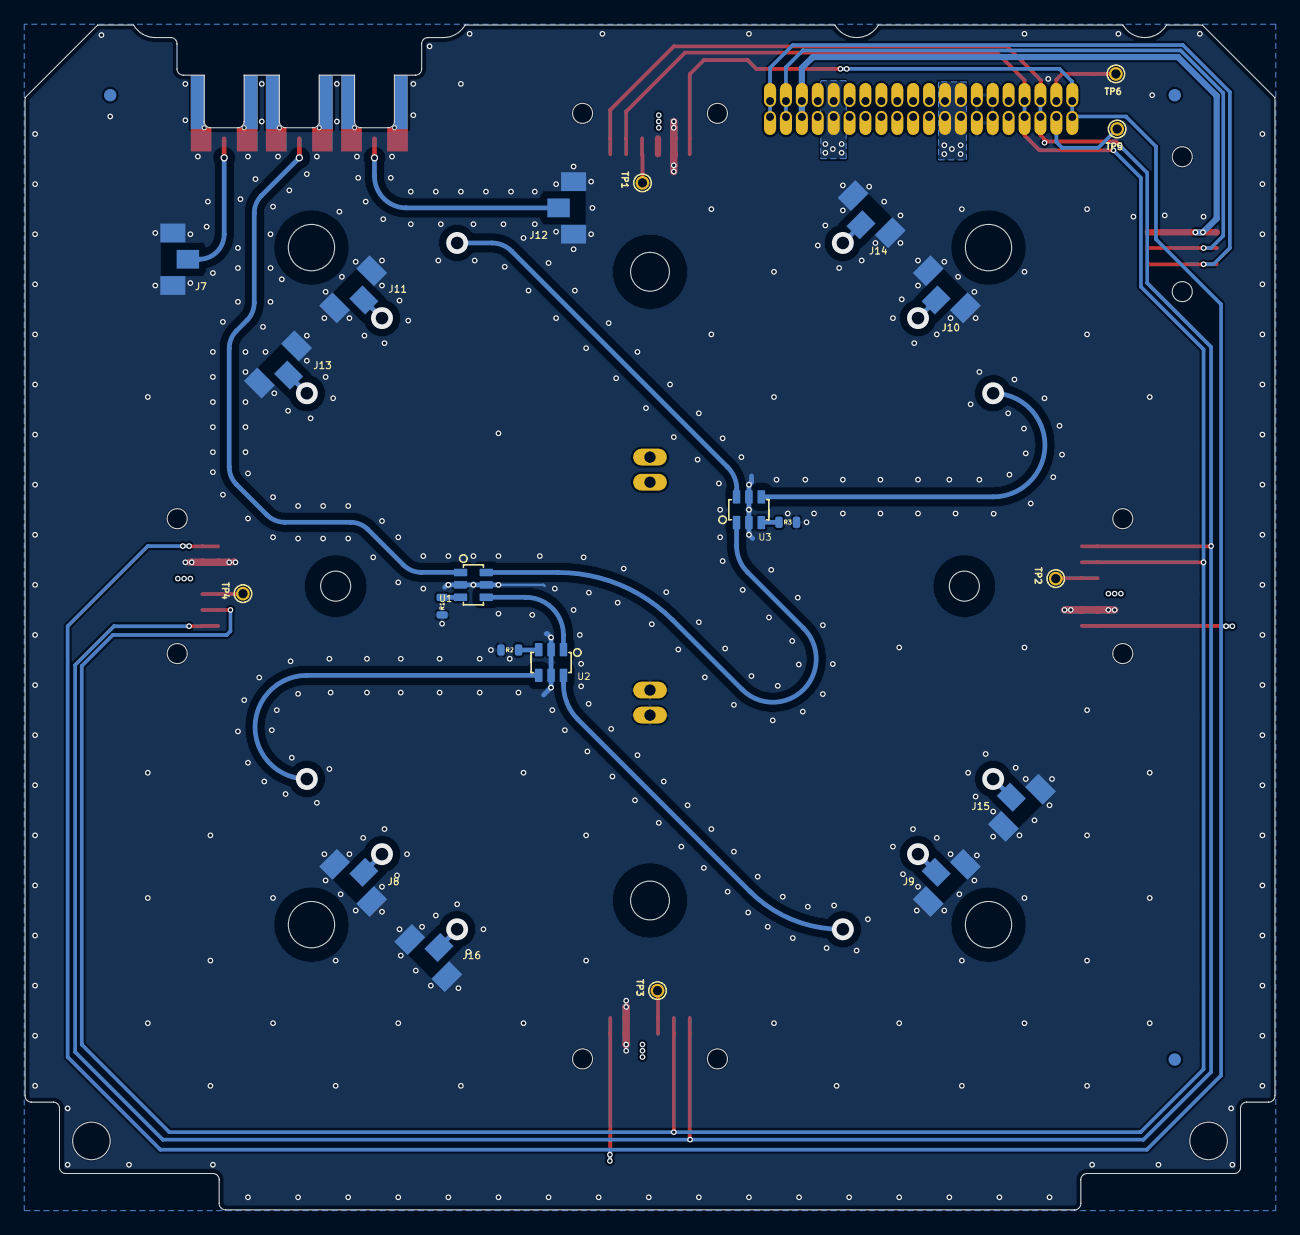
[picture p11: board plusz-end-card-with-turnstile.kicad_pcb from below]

Board: 4 copper layers, 99.8 x 94.6 mm, 48 parts (19 on the bottom side), 23 nets.

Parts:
CF1: J-HARWIN-M55-6001242R; HARWIN-M55-60X1242R
CM1, CM2, CM3: J-MOLEX-SMPM-73300-003X; J-MOLEX-SMPM-073300-003X
FIDUCIAL1, FIDUCIAL2, FIDUCIAL3, FIDUCIAL4, FIDUCIAL5, FIDUCIAL6: FIDUCIAL-1.0X2.0
HW1, HW2, HW3, HW4: MCMASTER-94100A150
J1, J2, J3, J4: Harwin M55-7101242R; M55-7101242R
J6: J-SAMTEC-TFM-120-X1-XXX-D-RA
J7, J8, J9, J10, J11, J12, J13, J14, J15, J16: R107064070_CONTACT
PCB1: ORESAT-CARD-V1.3-GENERIC-3RF
R1, R2, R3: 50; .0603-C-NOSILK
R5: 7.5 1W; PAC100-FOR-MELTWIRE
TP1, TP2, TP3, TP4, TP5, TP6: TEST-POINT-LARGE-SQUARE; 1X01
U1, U2, U3: QCN-19+; QCN-XXX+
U$1: FLIGHMARKERNEW; FLIGHTMARKER_NEW_BOARDS
UNK_HOLE_0: dummyfp0
UNK_HOLE_1: dummyfp1
UNK_HOLE_2: dummyfp2
UNK_HOLE_3: dummyfp3

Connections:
/CONNECTORS/C3-UART-RX: J6.38, TP5.1 (1_1)
/CONNECTORS/C3-UART-TX: J6.37, TP6.1 (1_1)
/CONNECTORS/CAN1_H: J1.9 (CANH), J1.10 (CANH), J2.9 (CANH), J2.10 (CANH), J3.9 (CANH), J3.10 (CANH), J4.9 (CANH), J4.10 (CANH), J6.33, J6.34
/CONNECTORS/CAN1_L: J1.11 (CANL), J1.12 (CANL), J2.11 (CANL), J2.12 (CANL), J3.11 (CANL), J3.12 (CANL), J4.11 (CANL), J4.12 (CANL), J6.35, J6.36
/CONNECTORS/MAG-POWER: CF1.5, CF1.6, J6.5, J6.6
/CONNECTORS/MAG-SCL: CF1.3, CF1.4, J6.3, J6.4
/CONNECTORS/MAG-SDA: CF1.1, CF1.2, J6.1, J6.2
/CONNECTORS/TURNSTILE-DEPLOY: J6.9, J6.10, R5.P$3 (2), R5.P$4 (2)
/CONNECTORS/VBUS: J1.5 (VBUS), J1.6 (VBUS), J2.5 (VBUS), J2.6 (VBUS), J3.5 (VBUS), J3.6 (VBUS), J4.5 (VBUS), J4.6 (VBUS), J6.23, J6.24, J6.25, J6.26
/CONNECTORS/~SD: J1.1 (~SD), J1.2 (~SD), J2.1 (~SD), J2.2 (~SD), J3.1 (~SD), J3.2 (~SD), J4.1 (~SD), J4.2 (~SD), J6.39, J6.40
/L1 BAND/RF-L1BAND: CM1.RF (CENTER), J12.P$1
/L BAND/RF-LBAND: CM2.RF (CENTER), U1.1 (SUM)
/L BAND/RF-LBAND-1/4L: U1.6 (PORT2), U3.1 (SUM)
/L BAND/RF-LBAND-SHORT: U1.4 (PORT1), U2.1 (SUM)
/UHF/RF-UHF: CM3.RF (CENTER), J7.P$1
GND: CF1.7, CF1.8, CF1.P$1 (SHIELDS), CF1.P$2 (SHIELDS), CF1.P$3 (SHIELDS), CF1.P$4 (SHIELDS), CM1.P$1 (SHIELD3), CM1.P$2 (SHIELD2), CM1.P$3 (SHIELD1), CM1.P$4 (SHIELD), CM2.P$1 (SHIELD3), CM2.P$2 (SHIELD2), CM2.P$3 (SHIELD1), CM2.P$4 (SHIELD), CM3.P$1 (SHIELD3), CM3.P$2 (SHIELD2), CM3.P$3 (SHIELD1), CM3.P$4 (SHIELD), J1.3 (GND), J1.4 (GND), J1.P$1 (SHIELD), J1.P$2 (SHIELD), J1.P$3 (SHIELD), J1.P$4 (SHIELD), J2.3 (GND), J2.4 (GND), J2.P$1 (SHIELD), J2.P$2 (SHIELD), J2.P$3 (SHIELD), J2.P$4 (SHIELD), J3.3 (GND), J3.4 (GND), J3.P$1 (SHIELD), J3.P$2 (SHIELD), J3.P$3 (SHIELD), J3.P$4 (SHIELD), J4.3 (GND), J4.4 (GND), J4.P$1 (SHIELD), J4.P$2 (SHIELD), J4.P$3 (SHIELD), J4.P$4 (SHIELD), J6.27, J6.28, J6.29, J6.30, J7.P$2, J7.P$3, J8.P$2, J8.P$3, J9.P$2, J9.P$3, J10.P$2, J10.P$3, J11.P$2, J11.P$3, J12.P$2, J12.P$3, J13.P$2, J13.P$3, J14.P$2, J14.P$3, J15.P$2, J15.P$3, J16.P$2, J16.P$3, R1.1, R2.1, R3.1, R5.P$1 (1), R5.P$2 (1), U1.2 (GND), U1.5 (GND), U2.2 (GND), U2.5 (GND), U3.2 (GND), U3.5 (GND)
unnamed: J1.7 (AUX), J1.8 (AUX), TP1.1 (1_1)
unnamed: J2.7 (AUX), J2.8 (AUX), TP2.1 (1_1)
unnamed: J3.7 (AUX), J3.8 (AUX), TP3.1 (1_1)
unnamed: J4.7 (AUX), J4.8 (AUX), TP4.1 (1_1)
unnamed: R1.2, U1.3 (TERM)
unnamed: R2.2, U2.3 (TERM)
unnamed: R3.2, U3.3 (TERM)

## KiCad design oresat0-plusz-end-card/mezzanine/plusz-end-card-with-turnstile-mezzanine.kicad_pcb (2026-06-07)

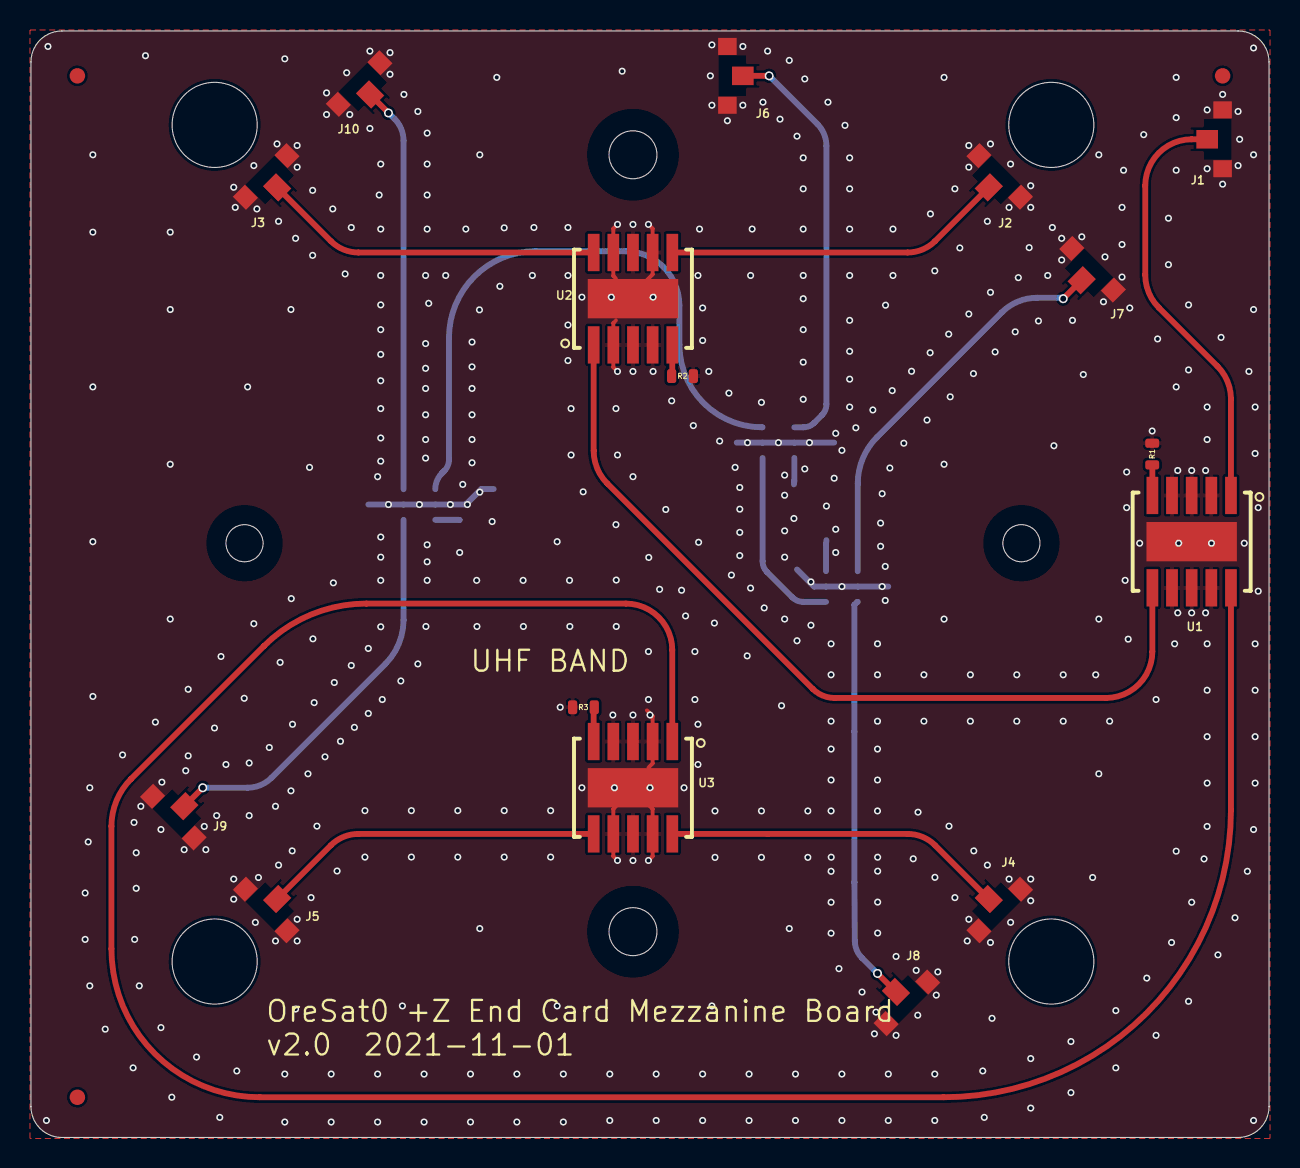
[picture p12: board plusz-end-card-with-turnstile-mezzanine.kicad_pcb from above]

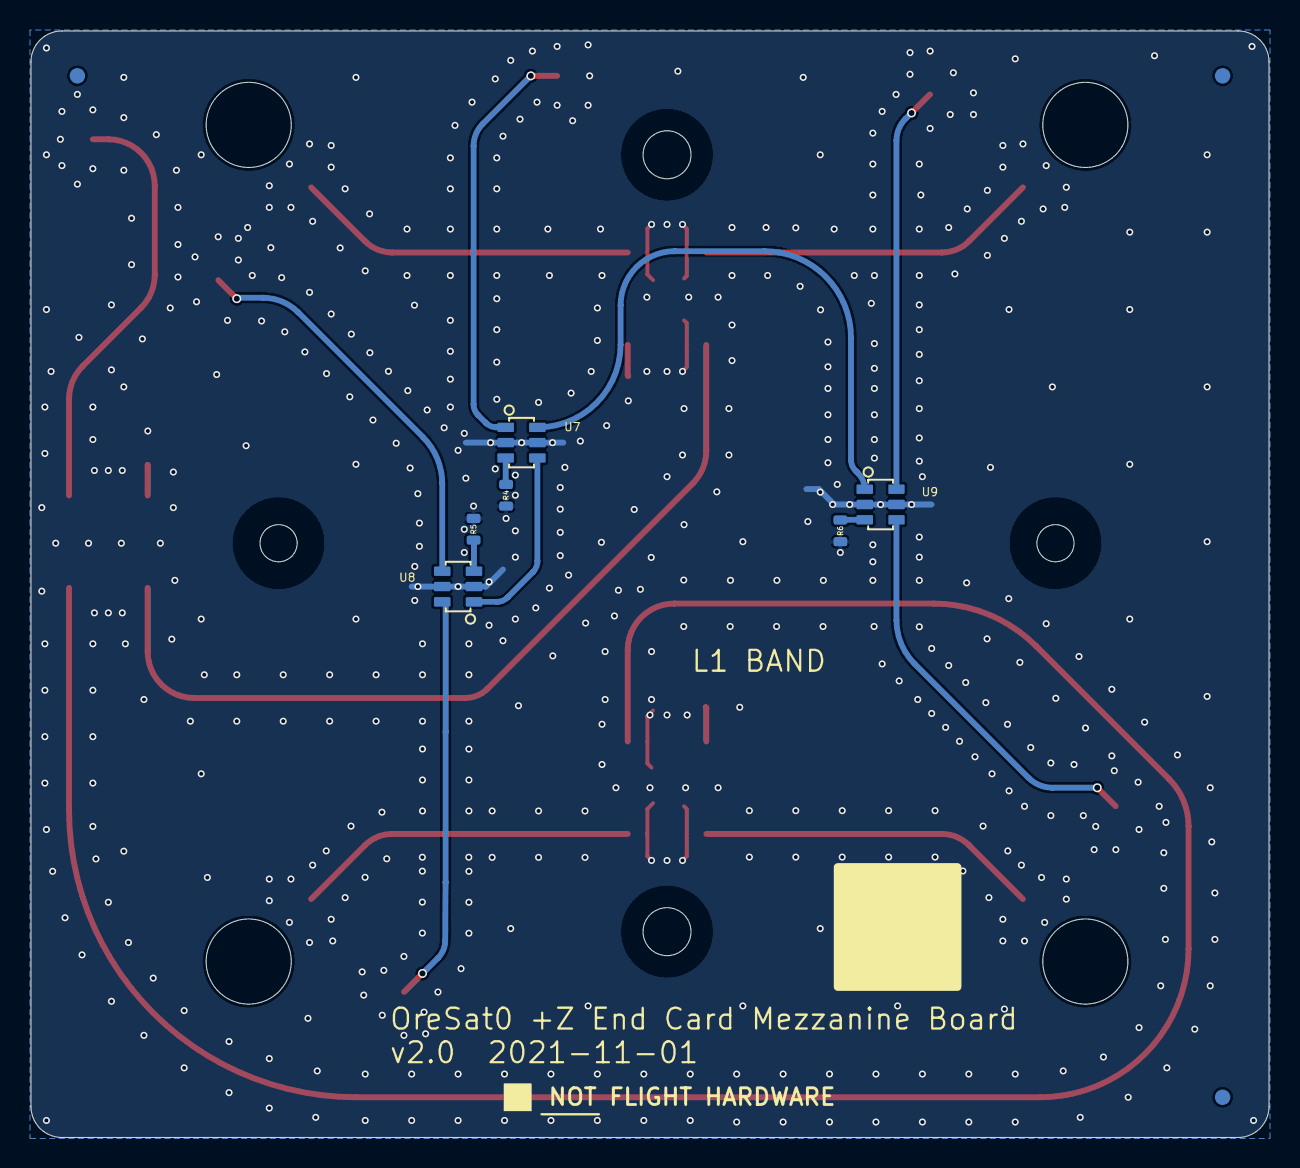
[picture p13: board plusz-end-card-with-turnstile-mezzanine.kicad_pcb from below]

Board: 4 copper layers, 80.0 x 71.5 mm, 37 parts (10 on the bottom side), 21 nets.

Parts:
FIDUCIAL1, FIDUCIAL2, FIDUCIAL3, FIDUCIAL4, FIDUCIAL6, FIDUCIAL7: FIDUCIAL-1.0X2.0
J1, J2, J3, J4, J5, J6, J7, J8, J9, J10: R107064070; R107064070_SOLDER
R1, R2, R3, R4, R5, R6: 50; .0603-C-NOSILK
U1, U2, U3: QBA-07+
U7, U8, U9: QCN-19+; QCN-XXX+
U$1: FLIGHMARKERNEW; FLIGHTMARKER_NEW_BOARDS
UNK_HOLE_0: dummyfp0
UNK_HOLE_1: dummyfp1
UNK_HOLE_2: dummyfp2
UNK_HOLE_3: dummyfp3
UNK_HOLE_4: dummyfp4
UNK_HOLE_5: dummyfp5
UNK_HOLE_6: dummyfp6
UNK_HOLE_7: dummyfp7

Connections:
GND: J1.P$2, J1.P$3, J2.P$2, J2.P$3, J3.P$2, J3.P$3, J4.P$2, J4.P$3, J5.P$2, J5.P$3, J6.P$2, J6.P$3, J7.P$2, J7.P$3, J8.P$2, J8.P$3, J9.P$2, J9.P$3, J10.P$2, J10.P$3, R1.1, R2.1, R3.1, R4.1, R5.1, R6.1, U1.2, U1.3, U1.4, U1.7, U1.8, U1.9, U1.GND-NO-PAD, U2.2, U2.3, U2.4, U2.7, U2.8, U2.9, U2.GND-NO-PAD, U3.2, U3.3, U3.4, U3.7, U3.8, U3.9, U3.GND-NO-PAD, U7.2, U7.5, U8.2, U8.5, U9.2, U9.5
L1BAND: J6.P$1, U7.1
L1BAND-SHORT: U7.4, U8.1
L1BAND-SHORT+1/4WAVE: U7.6, U9.1
L1BAND_0: J7.P$1, U8.4
L1BAND_90: J8.P$1, U8.6
L1BAND_180: J9.P$1, U9.4
L1BAND_270: J10.P$1, U9.6
unnamed: R4.2, U7.3
unnamed: R5.2, U8.3
unnamed: R1.2, U1.5
unnamed: R2.2, U2.5
unnamed: R6.2, U9.3
unnamed: R3.2, U3.5
UHF: J1.P$1, U1.1
UHF-SHORT: U1.6, U2.1
UHF-SHORT+1/4WAVE: U1.10, U3.1
UHF_0: J2.P$1, U2.6
UHF_90: J3.P$1, U2.10
UHF_180: J5.P$1, U3.6
UHF_270: J4.P$1, U3.10

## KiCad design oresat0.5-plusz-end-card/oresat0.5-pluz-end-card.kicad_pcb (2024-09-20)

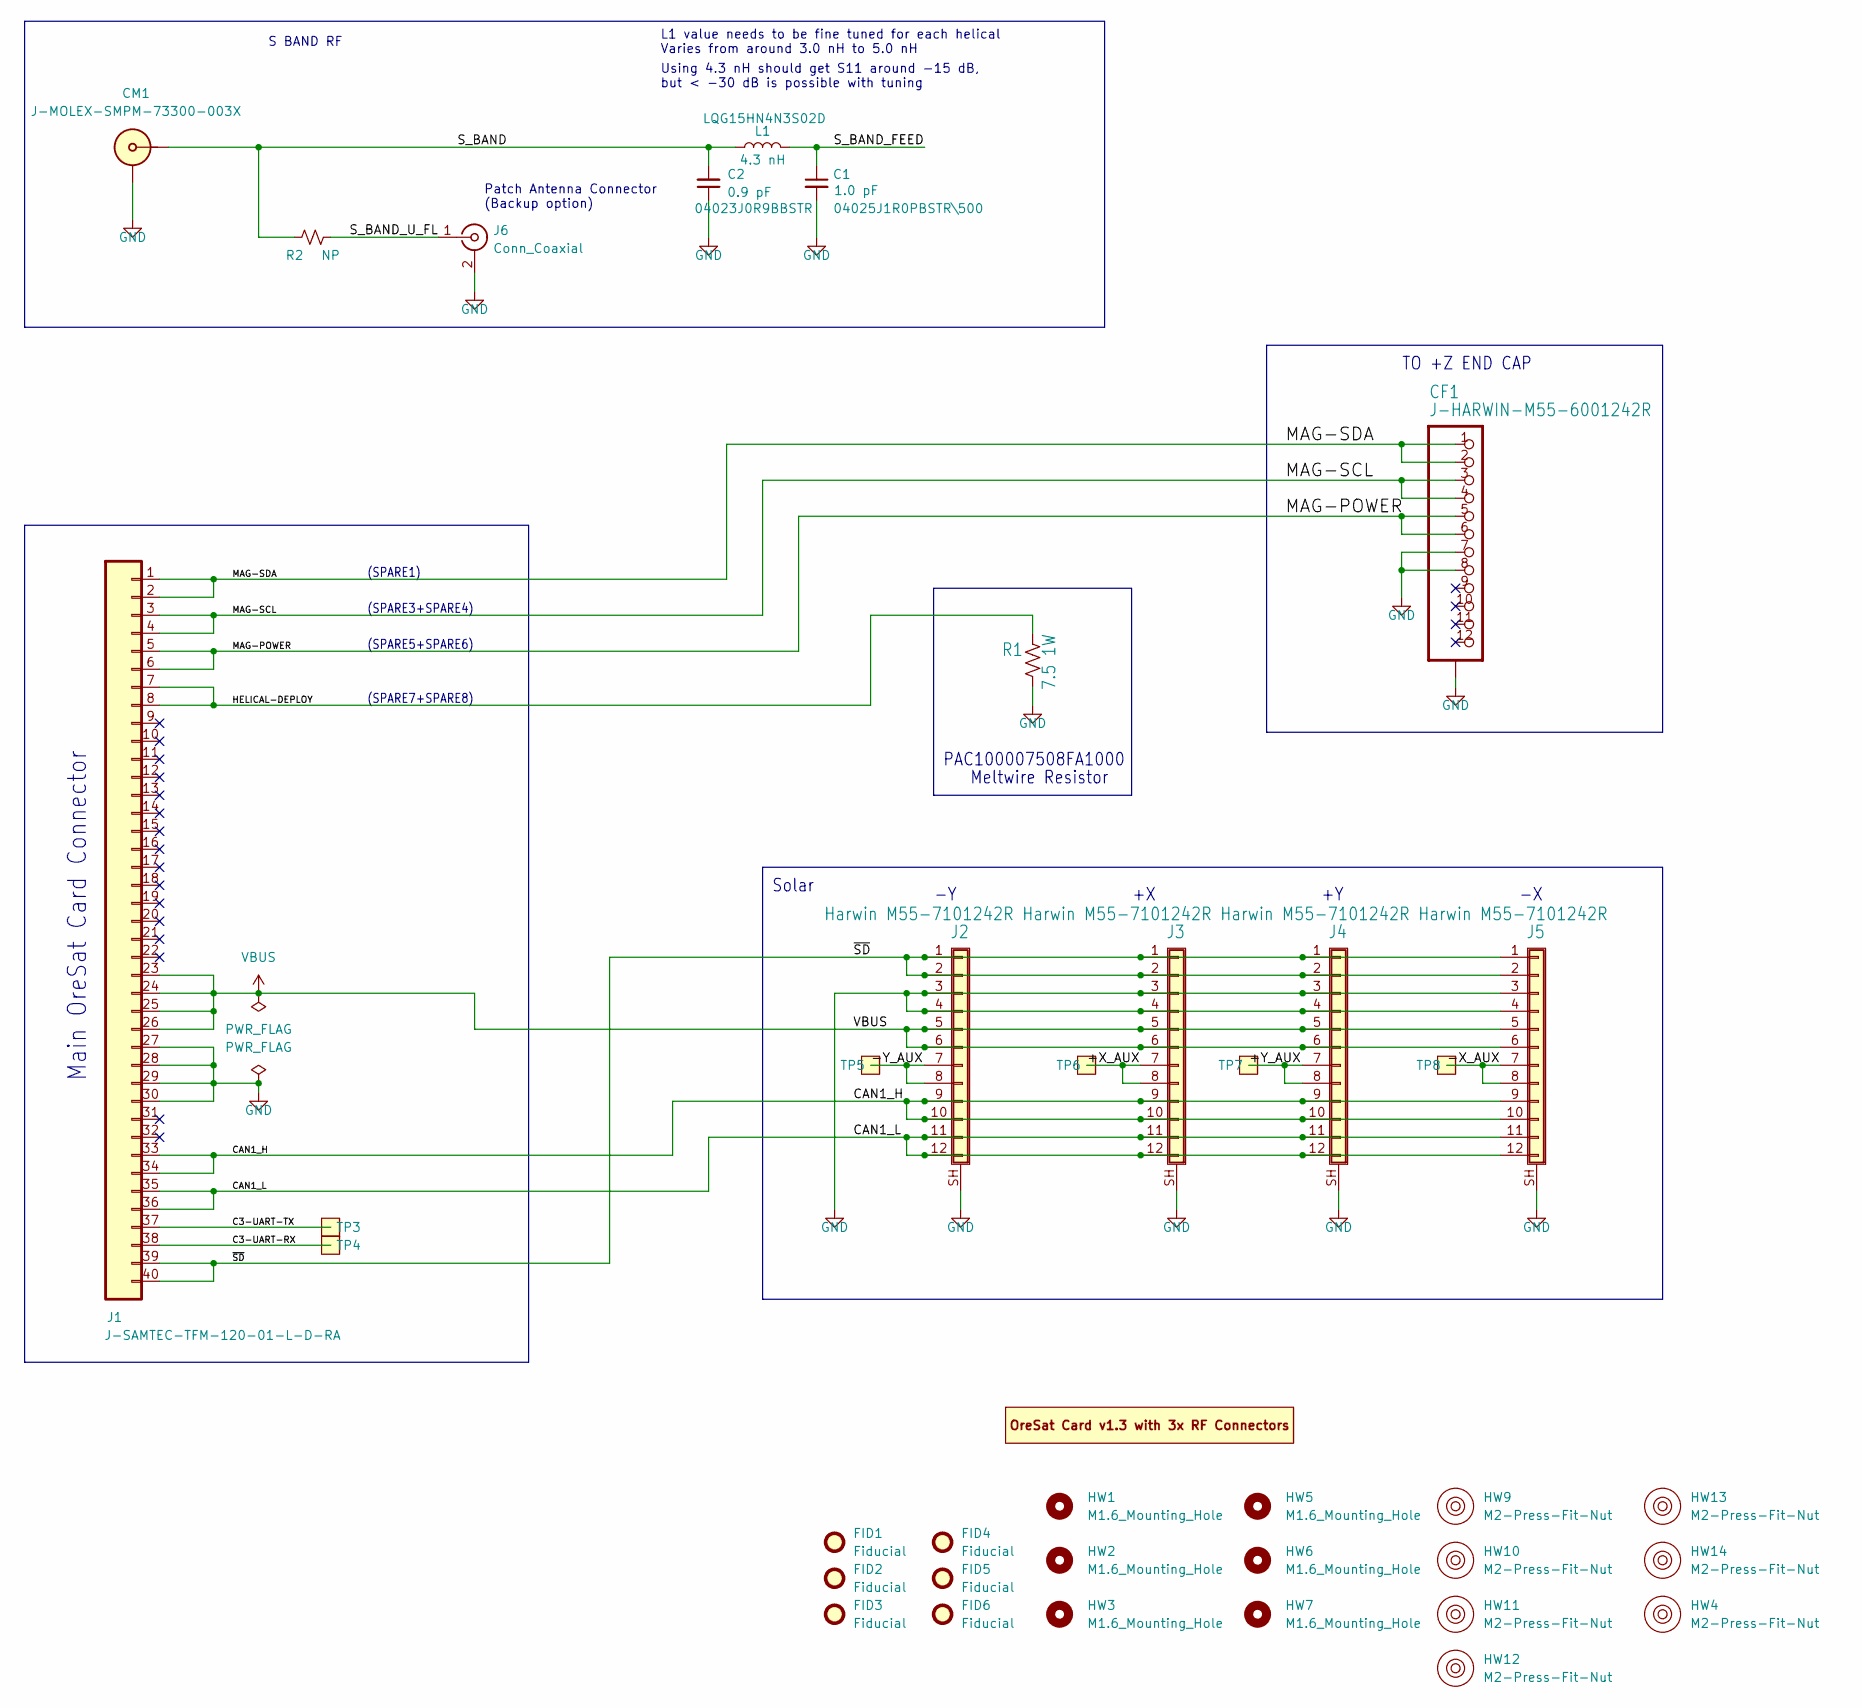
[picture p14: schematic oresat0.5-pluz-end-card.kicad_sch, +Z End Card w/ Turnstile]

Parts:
C1: 1.0 pF; C_0402_1005Metric; MPN 04025J1R0PBSTR\500
C2: 0.9 pF; C_0402_1005Metric; MPN 04023J0R9BBSTR
CF1: J-HARWIN-M55-6001242R; J-Harwin-M55-60X1242R; MPN M55-6021242R
CM1: J-MOLEX-SMPM-73300-003X; J-MOLEX-SMPM-073300-002X; MPN 952-3851-1-ND
FID1, FID2, FID3, FID4, FID5, FID6: Fiducial; Fiducial_1mm_Mask2mm
HW1, HW2, HW3, HW5, HW6, HW7: M1.6_Mounting_Hole; M1.6 Mounting Hole
HW4, HW9, HW10, HW11, HW12, HW13, HW14: M2-Press-Fit-Nut
J1: J-SAMTEC-TFM-120-01-L-D-RA; J-SAMTEC-TFM-120-X1-XXX-D-RA; MPN TFM-120-01-L-D-RA
J2, J3, J4, J5: Harwin M55-7101242R; J-Harwin-M55-7101242R; MPN M55-7101242R
J6: Conn_Coaxial; U.FL_Hirose_U.FL-R-SMT-1_Vertical; MPN U.FL-R-SMT-1(10)
L1: 4.3 nH; L_0402_1005Metric; MPN LQG15HN4N3S02D
PCB1: ORESAT-CARD-V1.3-GENERIC-3RF; ORESAT-CARD-V1.3-3RF
R1: 7.5 1W; R-PAC100-FOR-MELTWIRE; MPN PAC100007508FA1000
R2: NP; R_0402_1005Metric; MPN RMCF0603ZT0R00
TP3, TP4, TP5, TP6, TP7, TP8: TestPoint-MinTH; TestPoint-0.75mm-th

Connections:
/+X_AUX: J3.7, J3.8, TP6.1
/+Y_AUX: J4.7, J4.8, TP7.1
/-X_AUX: J5.7, J5.8, TP8.1
/-Y_AUX: J2.7, J2.8, TP5.1
/C3-UART-RX: J1.38, TP4.1
/C3-UART-TX: J1.37, TP3.1
/CAN1_H: J1.33, J1.34, J2.9, J2.10, J3.9, J3.10, J4.9, J4.10, J5.9, J5.10
/CAN1_L: J1.35, J1.36, J2.11, J2.12, J3.11, J3.12, J4.11, J4.12, J5.11, J5.12
/HELICAL-DEPLOY: J1.7, J1.8, R1.2
/MAG-POWER: CF1.5, CF1.6, J1.5, J1.6
/MAG-SCL: CF1.3, CF1.4, J1.3, J1.4
/MAG-SDA: CF1.1, CF1.2, J1.1, J1.2
/S_BAND: C2.2, CM1.SIG, L1.1, R2.1
/S_BAND_FEED: C1.1, L1.2
/S_BAND_U_FL: J6.1 (In), R2.2
/~SD: J1.39, J1.40, J2.1, J2.2, J3.1, J3.2, J4.1, J4.2, J5.1, J5.2
GND: C1.2, C2.1, CF1.7, CF1.8, CF1.SH (SHIELD), CM1.SHLD, J1.27, J1.28, J1.29, J1.30, J2.3, J2.4, J2.SH (Shield), J3.3, J3.4, J3.SH (Shield), J4.3, J4.4, J4.SH (Shield), J5.3, J5.4, J5.SH (Shield), J6.2 (Ext), R1.1
VBUS: J1.23, J1.24, J1.25, J1.26, J2.5, J2.6, J3.5, J3.6, J4.5, J4.6, J5.5, J5.6

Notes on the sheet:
TO +Z END CAP
(SPARE7+SPARE8)
L1 value needs to be fine tuned for each helical Varies from around 3.0 nH to 5.0 nH
Meltwire Resistor
Using 4.3 nH should get S11 around -15 dB, but < -30 dB is possible with tuning
S BAND RF
Solar
PAC100007508FA1000
(SPARE1)
(SPARE3+SPARE4)
Patch Antenna Connector (Backup option)
Main OreSat Card Connector
(SPARE5+SPARE6)

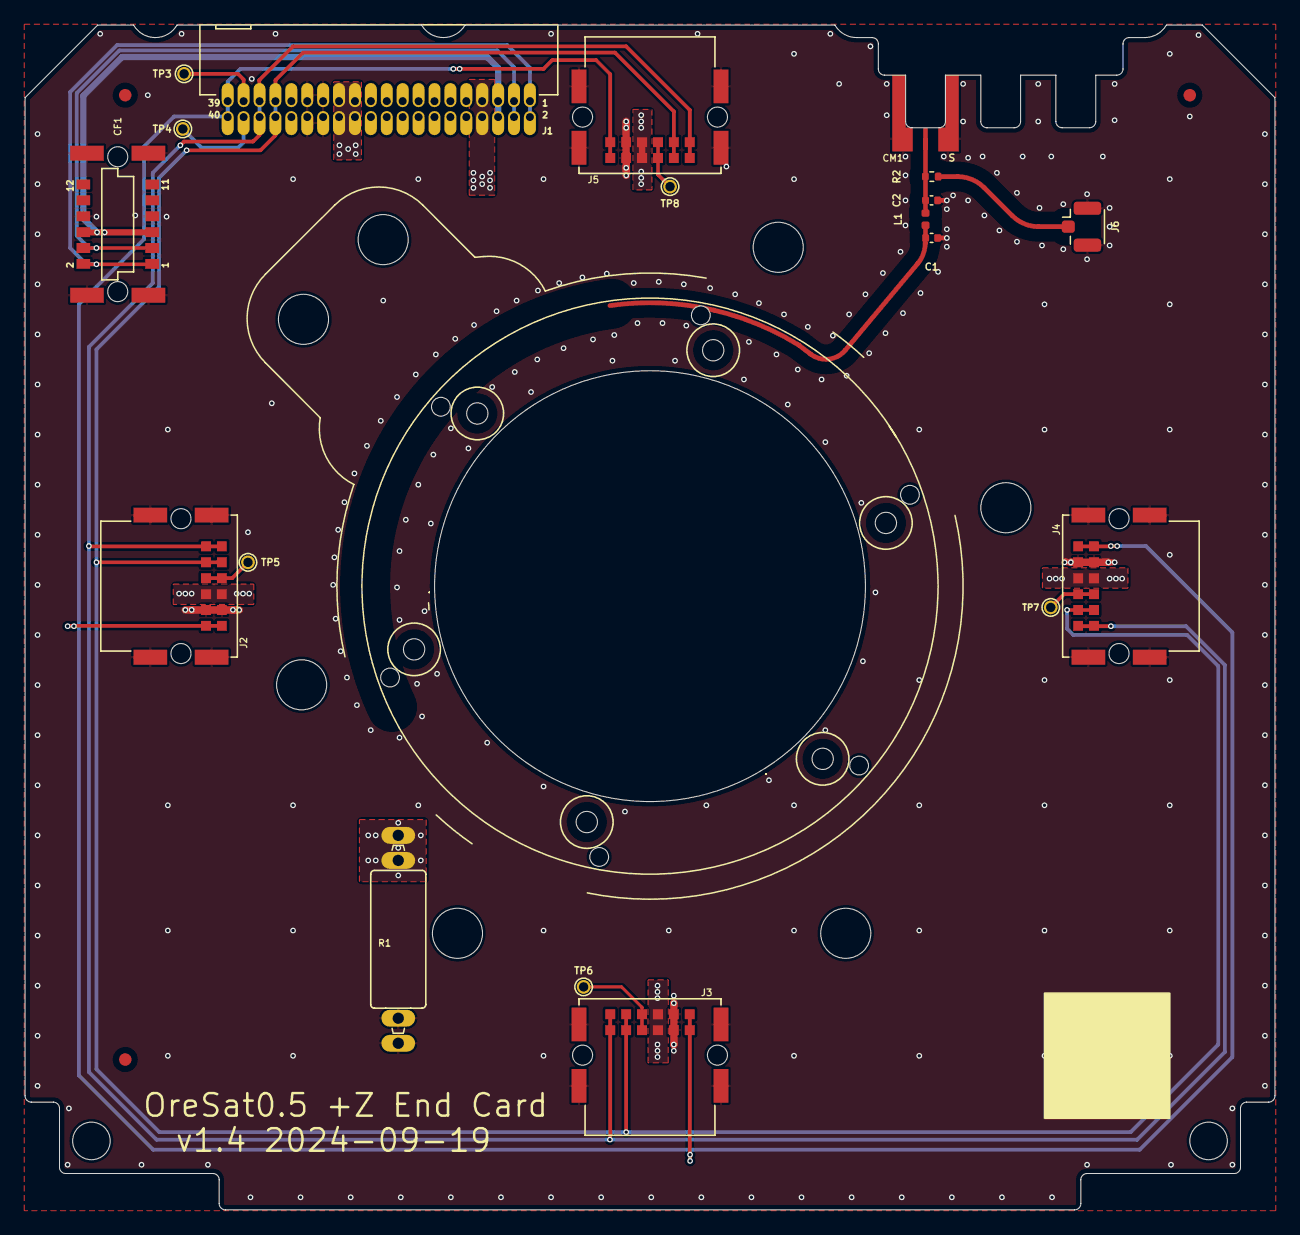
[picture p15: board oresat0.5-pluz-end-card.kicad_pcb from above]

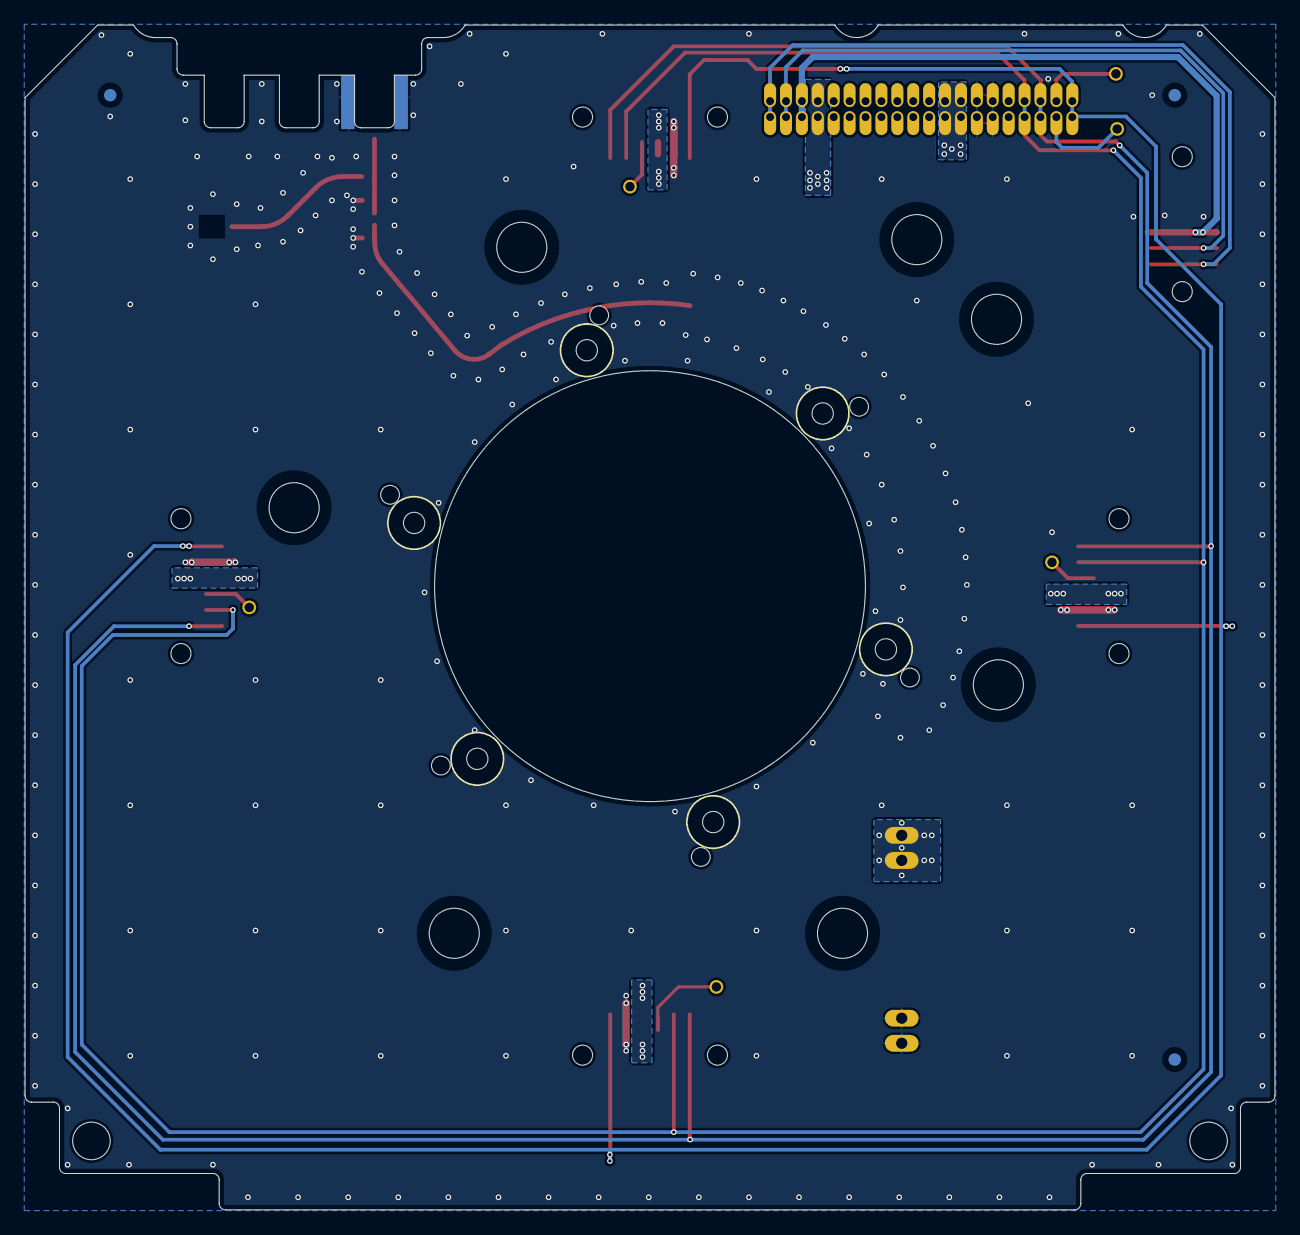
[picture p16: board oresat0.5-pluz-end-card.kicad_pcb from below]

Board: 4 copper layers, 99.8 x 94.6 mm, 39 parts (3 on the bottom side), 18 nets.

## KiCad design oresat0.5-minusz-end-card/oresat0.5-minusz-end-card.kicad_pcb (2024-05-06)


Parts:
CF1: J-HARWIN-M55-6001242R; J-Harwin-M55-60X1242R
CM1, CM2, CM3: J-MOLEX-SMPM-73300-003X; J-MOLEX-SMPM-073300-002X
FID1, FID2, FID3, FID4, FID5, FID6: Fiducial; Fiducial_1mm_Mask2mm
H101, H102, H103, H104, H105, H106, H107, H108: MountingHole; MountingHole_5mm
HW1, HW2, HW3, HW4, HW5, HW6: M2-Press-Fit-Nut
J1: J-SAMTEC-TFM-120-01-L-D-RA; J-SAMTEC-TFM-120-X1-XXX-D-RA
J2: U.FL-R-SMT-1; U.FL_Hirose_U.FL-R-SMT-1_Vertical
J3, J5: Harwin M55-7101242R; J-Harwin-M55-7101242R
J4, J6: tape-measure-slot-antenna
PCB1: ORESAT-CARD-V1.3-GENERIC-3RF; ORESAT-CARD-V1.3-3RF
R1: 7.5 1W; R-PAC100-FOR-MELTWIRE
TP1, TP2, TP4, TP6: TEST-POINT-LARGE-SQUARE; TestPoint-0.75mm-th

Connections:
/+X_AUX: J5.7, J5.8, TP6.1
/-X_AUX: J3.7, J3.8, TP4.1
/C3-UART-RX: J1.38, TP2.1
/C3-UART-TX: J1.37, TP1.1
/CAN1_H: J1.33, J1.34, J3.9, J3.10, J5.9, J5.10
/CAN1_L: J1.35, J1.36, J3.11, J3.12, J5.11, J5.12
/L1BAND: CM1.SIG, J2.1 (In)
/LBAND: CM2.SIG, J4.1
/MAG-POWER: CF1.5, CF1.6, J1.5, J1.6
/MAG-SCL: CF1.3, CF1.4, J1.3, J1.4
/MAG-SDA: CF1.1, CF1.2, J1.1, J1.2
/TURNSTILE-DEPLOY: J1.9, J1.10, R1.1
/UHF: CM3.SIG, J6.1
/~SD: J1.39, J1.40, J3.1, J3.2, J5.1, J5.2
GND: CF1.7, CF1.8, CF1.SH (SHIELD), CM1.SHLD, CM2.SHLD, CM3.SHLD, J1.27, J1.28, J1.29, J1.30, J2.2 (Ext), J3.3, J3.4, J3.SH (Shield), J5.3, J5.4, J5.SH (Shield), R1.2
VBUS: J1.23, J1.24, J1.25, J1.26, J3.5, J3.6, J5.5, J5.6

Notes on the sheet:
PAC100007508FA1000
(SPARE5+SPARE6)
(SPARE3+SPARE4)
(SPARE9+SPARE10)
Pass-through holes for M2 fasteners for CFC sensor heat sink assembly
TO +Z END CAP
Meltwire Resistor
To L band monopole
Main OreSat Card Connector
Press-fit nuts for monopole deployer and CFC lens holder
To UHF band monopole
(SPARE1)
UHF Feed System (436.5 MHz)
L1 (GPS) Band Feed System (1.57542 GHz)
To GPS antenna on -Z End Cap via U.FL to U.FL coax cable
L Band Feed System (1.265 GHz)
Solar



Board: 4 copper layers, 99.8 x 94.6 mm, 36 parts (13 on the bottom side), 16 nets.

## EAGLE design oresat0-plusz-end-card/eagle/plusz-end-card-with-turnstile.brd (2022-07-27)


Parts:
CF1: J-HARWIN-M55-6001242R; HARWIN-M55-60X1242R
FIDUCIAL1, FIDUCIAL2, FIDUCIAL3, FIDUCIAL4, FIDUCIAL5, FIDUCIAL6: FIDUCIAL-1.0X2.0
HW1, HW2, HW3, HW4: MCMASTER-94100A150
J1, J2, J3, J4: Harwin M55-7101242R; M55-7101242R
J6: J-SAMTEC-TFM-120-X1-XXX-D-RA; MPN TFM-120-01-L-D-RA
PCB1: ORESAT-CARD-V1.3-GENERIC-3RF
R5: 7.5 1W; PAC100-FOR-MELTWIRE
TP1, TP2, TP3, TP4, TP5, TP6: TEST-POINT-LARGE-SQUARE; 1X01
U$1: FLIGHMARKERNEW; FLIGHTMARKER_NEW_BOARDS

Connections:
!SD: J1.1 (!SD), J1.2 (!SD), J2.1 (!SD), J2.2 (!SD), J3.1 (!SD), J3.2 (!SD), J4.1 (!SD), J4.2 (!SD), J6.39, J6.40
C3-UART-RX: J6.38, TP5.1
C3-UART-TX: J6.37, TP6.1
CAN1_H: J1.9 (CANH), J1.10 (CANH), J2.9 (CANH), J2.10 (CANH), J3.9 (CANH), J3.10 (CANH), J4.9 (CANH), J4.10 (CANH), J6.33, J6.34
CAN1_L: J1.11 (CANL), J1.12 (CANL), J2.11 (CANL), J2.12 (CANL), J3.11 (CANL), J3.12 (CANL), J4.11 (CANL), J4.12 (CANL), J6.35, J6.36
GND: CF1.7, CF1.8, CF1.P$1 (SHIELDS), CF1.P$2 (SHIELDS), CF1.P$3 (SHIELDS), CF1.P$4 (SHIELDS), J1.3 (GND), J1.4 (GND), J1.P$1 (SHIELD), J1.P$2 (SHIELD), J1.P$3 (SHIELD), J1.P$4 (SHIELD), J2.3 (GND), J2.4 (GND), J2.P$1 (SHIELD), J2.P$2 (SHIELD), J2.P$3 (SHIELD), J2.P$4 (SHIELD), J3.3 (GND), J3.4 (GND), J3.P$1 (SHIELD), J3.P$2 (SHIELD), J3.P$3 (SHIELD), J3.P$4 (SHIELD), J4.3 (GND), J4.4 (GND), J4.P$1 (SHIELD), J4.P$2 (SHIELD), J4.P$3 (SHIELD), J4.P$4 (SHIELD), J6.27, J6.28, J6.29, J6.30, R5.P$1 (1), R5.P$2 (1); also elsewhere on the board
MAG-POWER: CF1.5, CF1.6, J6.5, J6.6
MAG-SCL: CF1.3, CF1.4, J6.3, J6.4
MAG-SDA: CF1.1, CF1.2, J6.1, J6.2
unnamed: J1.7 (AUX), J1.8 (AUX), TP1.1
unnamed: J2.7 (AUX), J2.8 (AUX), TP2.1
unnamed: J3.7 (AUX), J3.8 (AUX), TP3.1
unnamed: J4.7 (AUX), J4.8 (AUX), TP4.1
TURNSTILE-DEPLOY: J6.9, J6.10, R5.P$3 (2), R5.P$4 (2)
VBUS: J1.5 (VBUS), J1.6 (VBUS), J2.5 (VBUS), J2.6 (VBUS), J3.5 (VBUS), J3.6 (VBUS), J4.5 (VBUS), J4.6 (VBUS), J6.23, J6.24, J6.25, J6.26

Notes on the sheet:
Main OreSat Card Connector
OreSat0 +Z End Cap: Solar + Turnstile
2.0
TO +Z END CAP
PEMSERT nuts for meltwires
PAC100007508FA1000
Meltwire Resistor
Fiducials on front and back
(SPARE1)
(SPARE3+SPARE4)
(SPARE5+SPARE6)
(SPARE9+SPARE10)


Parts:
CM2: J-MOLEX-SMPM-73300-003X; J-MOLEX-SMPM-073300-003X
R1, R2, R3: 50; .0603-C-NOSILK
U1, U2, U3: QCN-19+; QCN-XXX+

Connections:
GND: CM2.P$1 (SHIELD3), CM2.P$2 (SHIELD2), CM2.P$3 (SHIELD1), CM2.P$4 (SHIELD), R1.1, R2.1, R3.1, U1.2 (GND), U1.5 (GND), U2.2 (GND), U2.5 (GND), U3.2 (GND), U3.5 (GND); also elsewhere on the board
LBAND: CM2.RF (CENTER), U1.1 (SUM)
LBAND-1/4L: U1.6 (PORT2), U3.1 (SUM)
LBAND-SHORT: U1.4 (PORT1), U2.1 (SUM)
LBAND_0: U2.4 (PORT1)
LBAND_90: U2.6 (PORT2)
LBAND_180: U3.4 (PORT1)
LBAND_270: U3.6 (PORT2)
unnamed: R1.2, U1.3 (TERM)
unnamed: R2.2, U2.3 (TERM)
unnamed: R3.2, U3.3 (TERM)

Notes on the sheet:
1/4 wavelength
L Band Feed System (1.265 GHz)
4x L Band Elements (through holes)
Length + 1/4L (+ 36.1 mm )
ALL WIRES MUST BE SAME LENGTH
1.265 GHz


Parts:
CM3: J-MOLEX-SMPM-73300-003X; J-MOLEX-SMPM-073300-003X
J7, J8, J9, J10, J11: R107064070_CONTACT

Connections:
GND: CM3.P$1 (SHIELD3), CM3.P$2 (SHIELD2), CM3.P$3 (SHIELD1), CM3.P$4 (SHIELD), J7.P$2, J7.P$3, J8.P$2, J8.P$3, J9.P$2, J9.P$3, J10.P$2, J10.P$3, J11.P$2, J11.P$3; also elsewhere on the board
UHF: CM3.RF (CENTER), J7.P$1
UHF_0: J11.P$1
UHF_90: J10.P$1
UHF_180: J9.P$1
UHF_270: J8.P$1

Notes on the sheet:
MEZZANINE PCB
UHF Feed System (436.5 MHz)
4x UHF elements (through holes)
ALL WIRES MUST BE SAME LENGTH


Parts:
CM1: J-MOLEX-SMPM-73300-003X; J-MOLEX-SMPM-073300-003X
J12, J13, J14, J15, J16: R107064070_CONTACT

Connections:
GND: CM1.P$1 (SHIELD3), CM1.P$2 (SHIELD2), CM1.P$3 (SHIELD1), CM1.P$4 (SHIELD), J12.P$2, J12.P$3, J13.P$2, J13.P$3, J14.P$2, J14.P$3, J15.P$2, J15.P$3, J16.P$2, J16.P$3; also elsewhere on the board
L1BAND: CM1.RF (CENTER), J12.P$1
L1BAND_0: J16.P$1
L1BAND_90: J15.P$1
L1BAND_180: J14.P$1
L1BAND_270: J13.P$1

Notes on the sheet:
MEZZANINE PCB
L1 BAND Feed System (1.575 GHz)
4x L1 elements (through holes)
ALL WIRES MUST BE SAME LENGTH



Board: 4 copper layers, 99.8 x 94.6 mm, 44 parts (19 on the bottom side), 23 nets.

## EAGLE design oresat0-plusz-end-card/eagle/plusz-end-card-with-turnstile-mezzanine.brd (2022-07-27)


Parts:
FIDUCIAL1, FIDUCIAL2, FIDUCIAL3, FIDUCIAL4, FIDUCIAL6, FIDUCIAL7: FIDUCIAL-1.0X2.0
J1, J2, J3, J4, J5: R107064070; R107064070_SOLDER
R1, R2, R3: 50; .0603-C-NOSILK
U1, U2, U3: QBA-07+
U$1: FLIGHMARKERNEW; FLIGHTMARKER_NEW_BOARDS

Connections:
GND: J1.P$2, J1.P$3, J2.P$2, J2.P$3, J3.P$2, J3.P$3, J4.P$2, J4.P$3, J5.P$2, J5.P$3, R1.1, R2.1, R3.1, U1.2 (GND), U1.3 (GND), U1.4 (GND), U1.7 (GND), U1.8 (GND), U1.9 (GND), U1.GND-NO-PAD (GND), U2.2 (GND), U2.3 (GND), U2.4 (GND), U2.7 (GND), U2.8 (GND), U2.9 (GND), U2.GND-NO-PAD (GND), U3.2 (GND), U3.3 (GND), U3.4 (GND), U3.7 (GND), U3.8 (GND), U3.9 (GND), U3.GND-NO-PAD (GND); also elsewhere on the board
unnamed: R1.2, U1.5 (TERM)
unnamed: R2.2, U2.5 (TERM)
unnamed: R3.2, U3.5 (TERM)
UHF: J1.P$1, U1.1 (SUM)
UHF-SHORT: U1.6 (0), U2.1 (SUM)
UHF-SHORT+1/4WAVE: U1.10 (90), U3.1 (SUM)
UHF_0: J2.P$1, U2.6 (0)
UHF_90: J3.P$1, U2.10 (90)
UHF_180: J5.P$1, U3.6 (0)
UHF_270: J4.P$1, U3.10 (90)

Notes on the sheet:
1/4 wavelength
v2.0
MEZZANINE BOARD UHF FEED SYSTEM (436.5 MHz)
MAKE SAME LENGTH
105 mm on 4 lyr OSH Park PCB


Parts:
J6, J7, J8, J9, J10: R107064070; R107064070_SOLDER
R4, R5, R6: 50; .0603-C-NOSILK
U7, U8, U9: QCN-19+; QCN-XXX+

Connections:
GND: J6.P$2, J6.P$3, J7.P$2, J7.P$3, J8.P$2, J8.P$3, J9.P$2, J9.P$3, J10.P$2, J10.P$3, R4.1, R5.1, R6.1, U7.2 (GND), U7.5 (GND), U8.2 (GND), U8.5 (GND), U9.2 (GND), U9.5 (GND); also elsewhere on the board
L1BAND: J6.P$1, U7.1 (SUM)
L1BAND-SHORT: U7.4 (PORT1), U8.1 (SUM)
L1BAND-SHORT+1/4WAVE: U7.6 (PORT2), U9.1 (SUM)
L1BAND_0: J7.P$1, U8.4 (PORT1)
L1BAND_90: J8.P$1, U8.6 (PORT2)
L1BAND_180: J9.P$1, U9.4 (PORT1)
L1BAND_270: J10.P$1, U9.6 (PORT2)
unnamed: R4.2, U7.3 (TERM)
unnamed: R5.2, U8.3 (TERM)
unnamed: R6.2, U9.3 (TERM)

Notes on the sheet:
1/4 wavelength
v1.1
L1 BAND FEED SYSTEM (1.575 GHz)
+29.1mm on 4 lyr OSH Park PCB
MAKE SAME LENGTH
1/4 wavelengh of the dielectric per oshpark 1.5742GHz



Board: 4 copper layers, 80.0 x 71.5 mm, 29 parts (10 on the bottom side), 21 nets.

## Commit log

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2018-12-17 Created library and placed solar connectors based on structure updates from yesterday.
    [oresat-plusz-end-card.brd, oresat-plusz-end-card.sch]
2018-12-19 Worked with Joe to check connectors, preliminary layout, 2 layers for now.
    [oresat-plusz-end-card.brd, oresat-plusz-end-card.sch]
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2019-02-26 Added debug board that comes off of the +Z and -Z end cards (past the caps).
    [debug-board.brd, debug-board.sch]
2019-02-26 Updated end cards with antenna keep outs, and rewired +Z end card debug port and started on +Z schematic update with power domain.
    [oresat-minusz-end-card.brd, oresat-minusz-end-card.sch, oresat-plusz-end-card.brd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]
2019-02-27 Added OreSat power domain -- via design blocksgit status -- and OMG it's doneish.
    [oresat-plusz-end-card.brd, oresat-plusz-end-card.sch]
2020-11-23 Moved OreSat0 +Z end card and mezzanine to the end card directory, where it really ought to have been. Updated the card and mezanine with Card outline v1.3, and added a first pass of the S band feed 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
    [debug-board.brd, debug-board.sch, oresat0-mezzanine.brd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]
2020-11-24 Final cleanup and polish of v1.1 OreSat0 +Z end card and mezzanine. Fixed S band 1/4 wave, lots of stiching and polish, fixed radial TCREAM on the contact pads, lots of TNAMES polish.
    [oresat0-mezzanine.brd, oresat0-mezzanine.sch, oresat0-plusz-end-card.brd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]
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2020-11-24 Switched to a QCN-27D+ (with DC passthrough) for S band, and made the U and L band 1/4 wave lengths a bit more precise after getting precise lengths from Eric.
    [oresat0-mezzanine.brd, oresat0-mezzanine.sch, oresat0-plusz-end-card-BOM.xlsx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]
2020-12-08 Small tweaks; reduced mezanine board size. Added flight tags. Off to fab!
    [oresat0-mezzanine.brd, oresat0-mezzanine.sch, oresat0-plusz-end-card.brd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]
2021-01-04 Forgot to remove a meltwire resistor.
    [oresat0-plusz-end-card-BOM.xlsx]
2021-04-08 Version 1.2 of the OreSat0 end card and mezzanine.
    Largest change is the position of the antennas on the end card; changes to the deployer changed the antenna placement which triggered everything else.
    Other changes include fiducials, attributes cleanup, move to 0603 resistors, and misc polish.
    [oresat0-mezzanine.brd, oresat0-mezzanine.sch, oresat0-plusz-end-card-BOM.xlsx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]
2021-04-21 Fixed bad part number for end card to end cap connector.
    [oresat0-plusz-end-card-BOM.xlsx, oresat0-plusz-end-card.brd, oresat0-plusz-end-card.sch]
2021-10-03 replaced S-band net labels with L1-band labels, swapped the S-band hybrids with L-band hybrids, recalculated 1/4 wavelength trace length, routed a new short+1/4 wavelength trace
    [oresat0-mezzanine.brd, oresat0-mezzanine.sch, oresat0-plusz-end-card.brd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]
2021-10-10 added vias along new short+1/4wave trace
    [oresat0-mezzanine.brd]
2021-10-10 added bstop new short+1/4wave trace
    [oresat0-mezzanine.brd]
2021-10-10 adjusted the length of L1BAND_0 and L1BAND_90 to match L1BAND_180 and L1BAND_270
    [oresat0-mezzanine.brd]
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2021-11-04 v2.0 card, mezzanine, and BOM for v2.0. Moved UHF hybrids to avoid melt wire resistor leads. Updated BOM to reflect new v2.0 design.
    [oresat0-mezzanine.brd, oresat0-mezzanine.sch, oresat0-plusz-end-card-BOM.xlsx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]
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2022-07-27 Move OreSat0 +Z end card to its own directory; removed amazingly old end cards that aren't relevant anymore.
    [oresat-minusz-end-card.brd, oresat-minusz-end-card.sch, oresat-plusz-end-card.brd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]
2022-07-27 Fixed some errors on the ancient -z end card
    [oresat-minusz-end-card.kicad_pcb, oresat-minusz-end-card.kicad_sch]
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2023-02-19 First rev of OreSat0.5 +Z end card. Updated helical deployer, removed as much EAGLE cruft as easily possible, killed multiple sch sheets.
    [CONNECTORS.kicad_sch, L1_BAND.kicad_sch, L_BAND.kicad_sch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]
2023-02-20 More KiCADing, new fiducials and footprints, fixed ERC and DRC. Now waiting on Cesar to do stuff.
    [plusz-end-card-generic.kicad_pcb, plusz-end-card-generic.kicad_sch]
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2023-02-20 Fixed +Z end card backplane connector library warning
    [oresat0.5-pluz-end-card.kicad_pcb]
2023-02-20 Updated -Z end card and replaced eagle imported libraries with kicad libraries
    [CONNECTORS.kicad_sch, L1_BAND.kicad_sch, L_BAND.kicad_sch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]
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2023-02-21 Added helical landing pad and left hopefully enough room for Garrett to put in matching components.
    [oresat0.5-pluz-end-card.kicad_pcb, oresat0.5-pluz-end-card.kicad_sch]
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2023-02-21 added Matching Components
    Added matching components for s band antenna, ground stitching
    [oresat0.5-pluz-end-card.kicad_pcb, oresat0.5-pluz-end-card.kicad_sch]
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2023-02-21 OMG what happened to the names of this card? Fixing.
    [minusz-end-card-oresat0-B_Cu.gbr, minusz-end-card-oresat0-B_Mask.gbr, minusz-end-card-oresat0-B_Paste.gbr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]
2023-02-21 fix silkscreen for -z end card
    [minusz-end-card-generic.kicad_pcb]
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2023-07-17 Updated OreSat 0.5 end card board outlines and mounting holes, and fixed KiCad library warnings
    [CONNECTORS.kicad_sch, L1_BAND.kicad_sch, L_BAND.kicad_sch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]
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2023-09-15 Fixed up OreSat0.5 -Z end card: Added hole for U.FL connector to get to GPS antnena, fixed library paths which seemed broken, replaced older EAGLE files too, fixed schematic/board disconnect with ref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
    [CONNECTORS.kicad_sch, L1_BAND.kicad_sch, L_BAND.kicad_sch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]
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2023-09-15 Fixed mispelling in name
    [CONNECTORS.kicad_sch, L1_BAND.kicad_sch, L_BAND.kicad_sch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]
2023-12-15 Moves antenna connection from large vias to slots so we don't need an a lead on the 1/4 inch tape measure antennas.
    [oresat0.5-minusz-end-card.kicad_pcb, oresat0.5-minusz-end-card.kicad_sch]
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2024-04-01 Updated date and unecessary polish on planes, including fillets and just more planes with more vias.
    [oresat0.5-minusz-end-card.kicad_pcb, oresat0.5-minusz-end-card.kicad_sch]
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2024-05-06 Added M2 fastener holes back into the -Z end card. Rev'd to v1.4.
    [oresat0.5-minusz-end-card.kicad_pcb, oresat0.5-minusz-end-card.kicad_sch]
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2024-08-20 Revert "initial mounting holes changes for new deployer" -- oops, wrong end card.
    This reverts commit 281d3ddd2ce643add95357c75bebd497bf0c76a9.
    [oresat0.5-minusz-end-card.kicad_pcb]
2024-08-20 Updated hole positions for single door deployer. TODO: fix weird net class errors that shouldn't exist.
    [oresat0.5-pluz-end-card.dxf, oresat0.5-pluz-end-card.kicad_pcb, oresat0.5-pluz-end-card.kicad_sch]
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2024-09-11 fixed silkscreen, fixed resistor helical deployer zone
    [oresat0.5-pluz-end-card.kicad_pcb]
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2024-09-20 Final polish for v1.4. Added more stiching vias, cleaned up some DRCs that were stupid, added more layers to deployment resistor pads, now sending off to Osh Park.
    [oresat0.5-pluz-end-card.kicad_pcb]
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2026-01-11 Creating OreSat1 end card folder for Spencer to start adding OPD deployer circuitry. Also probably needs updates for +Z end card for new helical deployer.
    [oresat1-minusz-end-card.kicad_pcb, oresat1-minusz-end-card.kicad_sch, oresat1-plusz-end-card.kicad_pcb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]
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2026-02-01 add OPD and deployer circuitry, some fixes needed
    [oresat1-minusz-end-card.kicad_pcb]
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2026-02-24 OreSat1 -Z end card update
    Upgraded symbols, fixed BOM and added presets, and added UART switches for new solar modules. Clleaned up layout, including some planes and footprints. Still more left to do, but it's more ready to go.
    [oresat1-minusz-end-card-sch-opd.kicad_sch, oresat1-minusz-end-card.kicad_pcb, oresat1-minusz-end-card.kicad_sch]
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2026-03-02 Started RF tracing, not complete -- maybe need to move the balun b/c microstrip turns are too sharp
    [ESI_minusz _end_card_v1.kicad_pcb]
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2026-03-06 Finalized dipole changes, added -/+ Y solar mods. Believe this is finished
    [esi-minusz-end-card-sch-opd.kicad_sch, esi-minusz-end-card.kicad_pcb, esi-minusz-end-card.kicad_sch]
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2026-03-09 Fixed schematic label issues and routed solar uarts
    [oresat1-plusz-end-card-sch-opd.kicad_sch, oresat1-plusz-end-card.kicad_pcb, oresat1-plusz-end-card.kicad_sch]
2026-03-09 fixed shcematic issues and routing, updated footprints
    [oresat1-plusz-end-card.kicad_pcb, oresat1-plusz-end-card.kicad_sch]
2026-03-09 mounting hole parity fix (internal screaming)
    [oresat1-plusz-end-card.kicad_pcb]
2026-03-10 is it fixed?
    [oresat1-plusz-end-card.kicad_pcb]
2026-03-10 Fixed weird footprint sync error that kept popping up on DRC around the mounting holes because of the polygon zone keepout areas. Also found a huge mistake in the schematic, fixed, still needs to be 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
    [oresat1-plusz-end-card.kicad_pcb, oresat1-plusz-end-card.kicad_sch]
2026-03-10 Whoops, fixed silly ERC errors
    [oresat1-plusz-end-card.kicad_sch]
2026-03-11 Fixed HW errors
    [oresat1-plusz-end-card.kicad_pcb]
2026-03-11 Fixed OPD connection in schematics and updated tracing and out of date footprints. Ready for final review from andrew
    [esi-minusz-end-card.kicad_pcb, esi-minusz-end-card.kicad_sch, oresat1-plusz-end-card.kicad_sch]
2026-03-11 FIxed OPD connection
    [oresat1-minusz-end-card.kicad_pcb, oresat1-minusz-end-card.kicad_sch]
2026-03-11 added clearance around HW
    [oresat1-plusz-end-card.kicad_pcb, oresat1-plusz-end-card.kicad_sch]
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2026-03-12 Another round on the +Z End Card; ready for fab.
    Brushed up RF paths and solder mask, cleaned up UART switches with closer bypass caps, cleaned up a lot of the zones, and lots of little polishing.
    [oresat1-plusz-end-card-sch-opd.kicad_sch, oresat1-plusz-end-card.kicad_pcb, oresat1-plusz-end-card.kicad_sch]
2026-03-15 Align SMPM connectors better and add a bit more solder mask keepout
    [oresat1-plusz-end-card.kicad_pcb]
2026-03-24 v1.1 sent to fab
    Updated 3D models of connectors, added missing capacitors, fixed footprints, polished schematic, upgraded to single README file with Makefile.
    [oresat1-plusz-end-card-sch-opd.kicad_sch, oresat1-plusz-end-card.kicad_pcb, oresat1-plusz-end-card.kicad_sch]
2026-04-13 ESI v1.0 -Z End Card for fab
    Added makefile and readme, fixed BOM error, moved to better RF zone rules
    [esi-minusz-end-card-sch-opd.kicad_sch, esi-minusz-end-card.kicad_pcb, esi-minusz-end-card.kicad_sch]
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2026-06-07 ESI -Z End Card updated to v1.1 with extremely minor changes (KiCad 10 update)
    Updated to KiCad 10.0.3, which updated several footprints and re-triggered from ERC
    and DRCs. Those were fixed, and out of an abundance of caution, we upped the version
    number although there's no significant difference with v1.0.
    [esi-minusz-end-card-sch-opd.kicad_sch, esi-minusz-end-card.kicad_pcb, esi-minusz-end-card.kicad_sch]
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2026-06-26 Swapped L and L1 Bands
    [esi-minusz-end-card.kicad_pcb, esi-minusz-end-card.kicad_sch]
